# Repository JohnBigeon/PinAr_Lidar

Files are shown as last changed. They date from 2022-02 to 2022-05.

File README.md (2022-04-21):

# PinAr_Lidar

<p float="left">
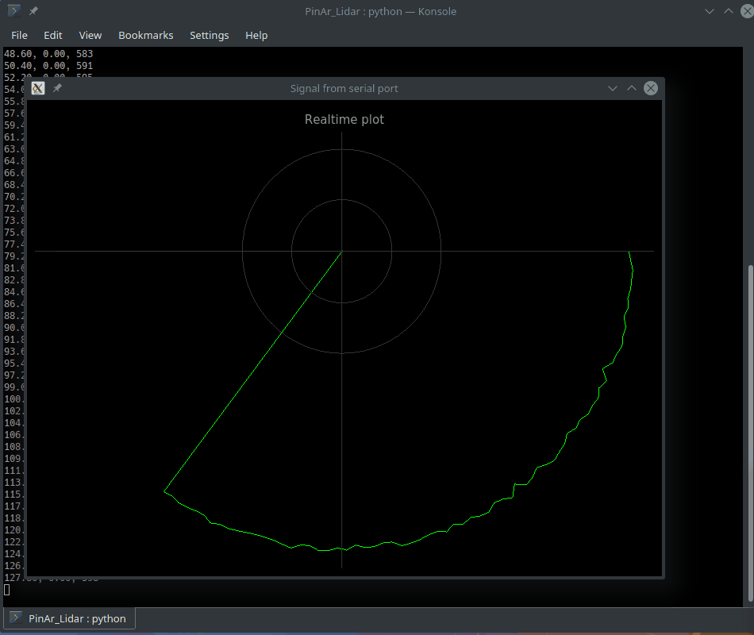
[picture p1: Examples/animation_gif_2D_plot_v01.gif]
  
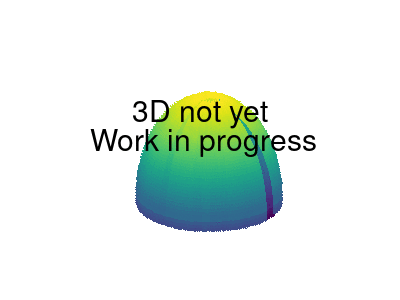
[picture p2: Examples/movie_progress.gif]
   
</p>

<p float="center">
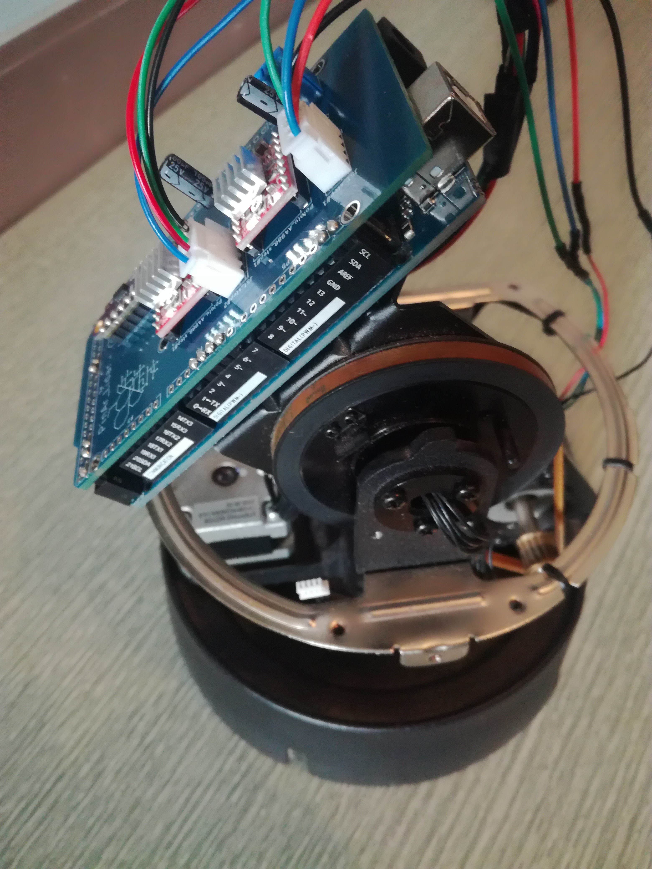
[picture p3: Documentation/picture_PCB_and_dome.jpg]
  
</p>

## Introduction
Here, we will build/assemble a three-dimensional mapping device from a CCTV dome camera setup and a Time-of-Flight (TOF) Distance Sensor to make 2D/3D cartography.

The first question: *Why “hack” a dome camera ?*

First answer, because a dome security camera is designed to monitor a wide range of angles (+/- 360° and +/- 180°). When you open it, you can find two stepper motors with belts, pulleys, and sprockets. All the mechanical parts can be easily hacked to use them as a base for your 2D positionning during cartography of your environment. Second answer, and maybe the best one, this dome was destined for the trash can. In other words, we decide to give a new life to something that will eventually be destroyed.

## Concept
From a pedagogical perspective, let’s start with a static problem. To make a long story short, a TOF setup calculates the distance to an object using time of flight. The time-of-flight principle is based on the time difference between the emission of a signal and its return to the sensor, after being reflected by an object, as presented below. Practically speaking, when a light is emitted from the source, this light will travel through the air until it hits an obstacle which reflects this light. In this case, the time between the emission and the reception is directly related to the distance.

<p float="center">
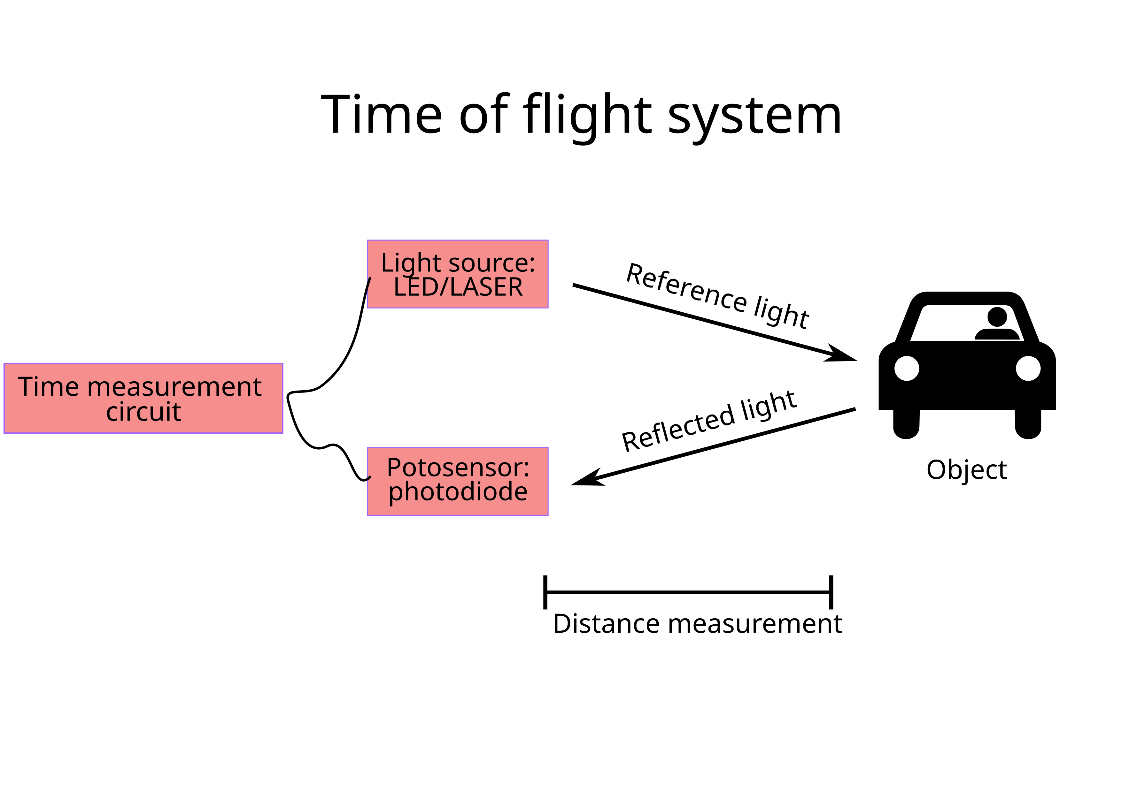
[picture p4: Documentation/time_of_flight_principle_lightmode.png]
  
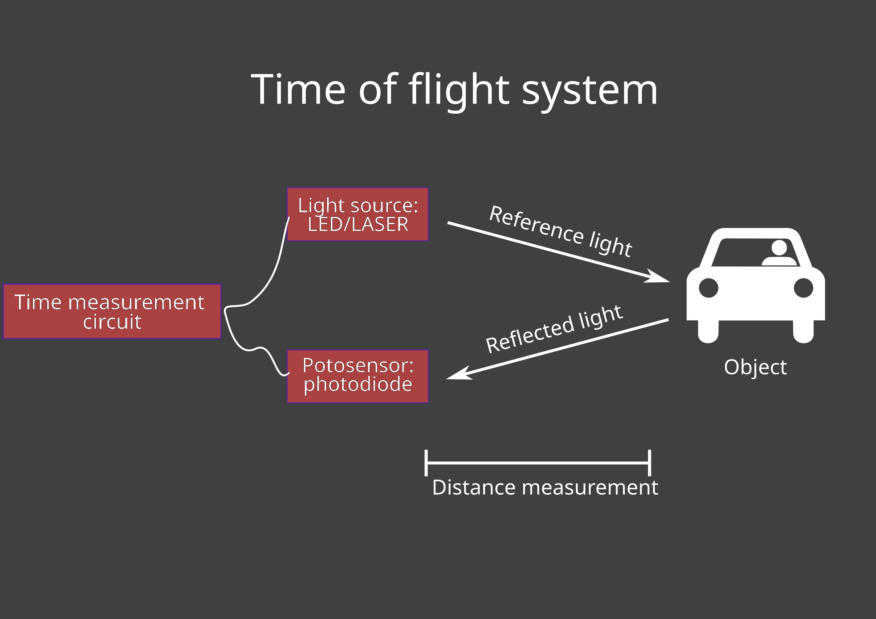
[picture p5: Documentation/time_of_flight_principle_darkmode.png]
  
</p>

Now, aim this source all around you at equally spaced intervals in both the zenithal (theta) and azimuthal (Phi) directions and you can fully determine the distance of objects around you. This is how most of Laser imaging, detection, and ranging (LIDAR) [https://en.wikipedia.org/wiki/Lidar] cartography is done.

From a practical view, the telemetry information is obtained by a Time-of-Flight Distance Sensor (VL5353LXX-V2) and the positioning in the two angular directions sweeping 360 and 180 degrees respectively is achieved by the two stepper motors of the dome system with microstepping driver (Pololu A4988).

## Hardware & Integration
### Dome security camera
<p float="left">
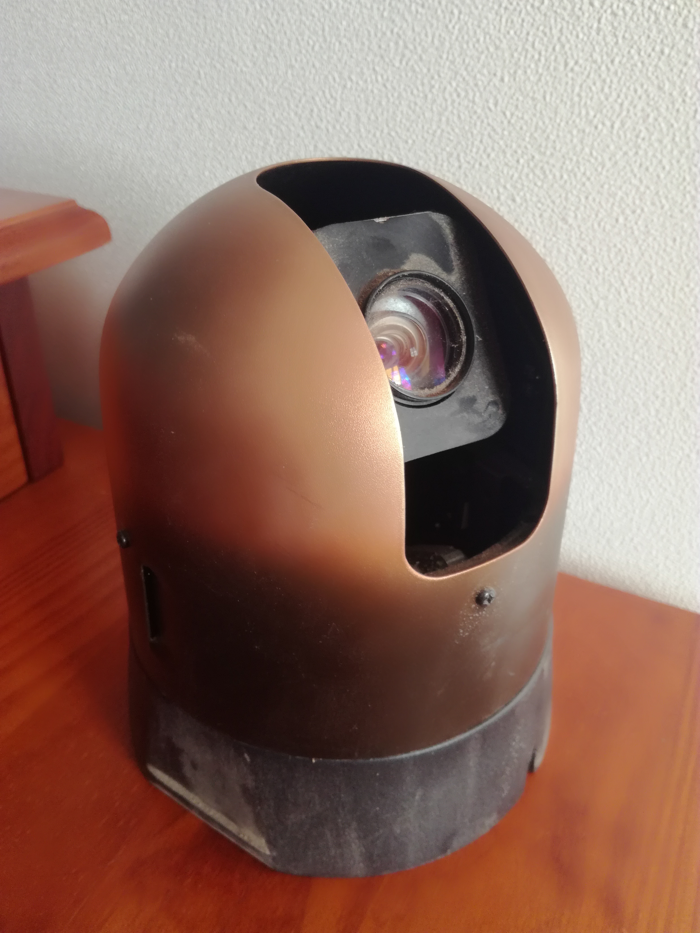
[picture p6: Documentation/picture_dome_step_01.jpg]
  
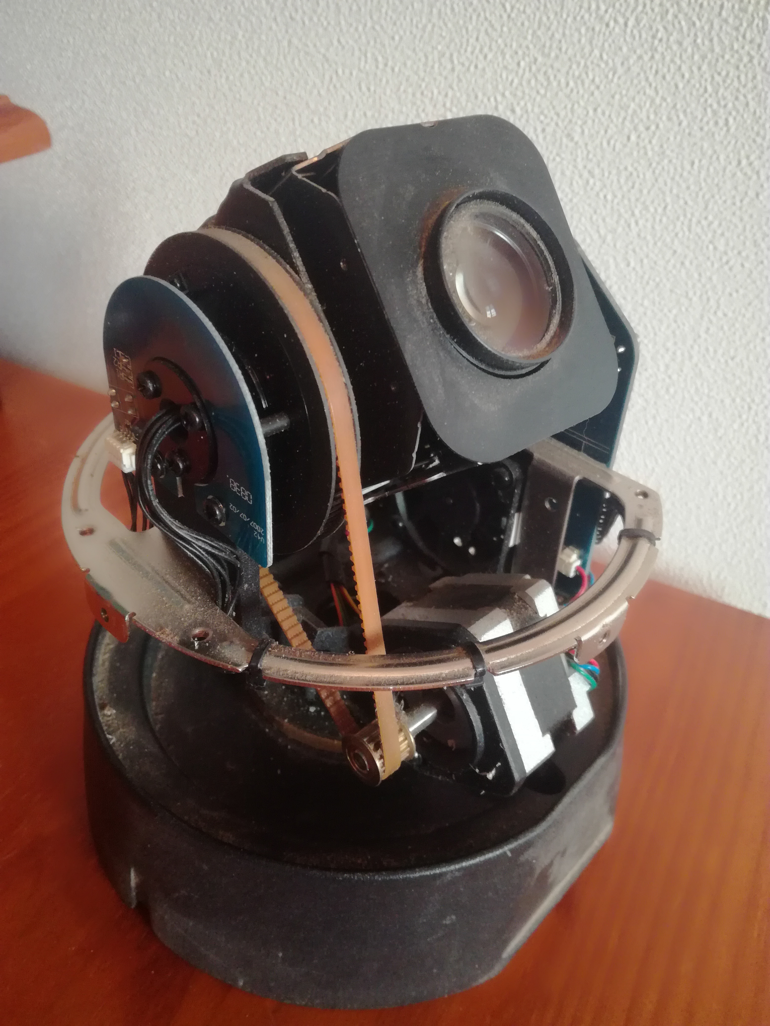
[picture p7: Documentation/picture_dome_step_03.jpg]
   
</p>

### Price
```
         Object           Price (€)
-----------------------   -----
            Arduino MEGA - 18
         Rotation system - 0 
     Power supply 12V 2A - 10
            Pololu A4988 - 3.50
 AZDelivery VL5353LXX-V2 - 9
    Capacitors ( 100 µF) - 1
                  Cables - 1
```
### Motors
<p float="left">
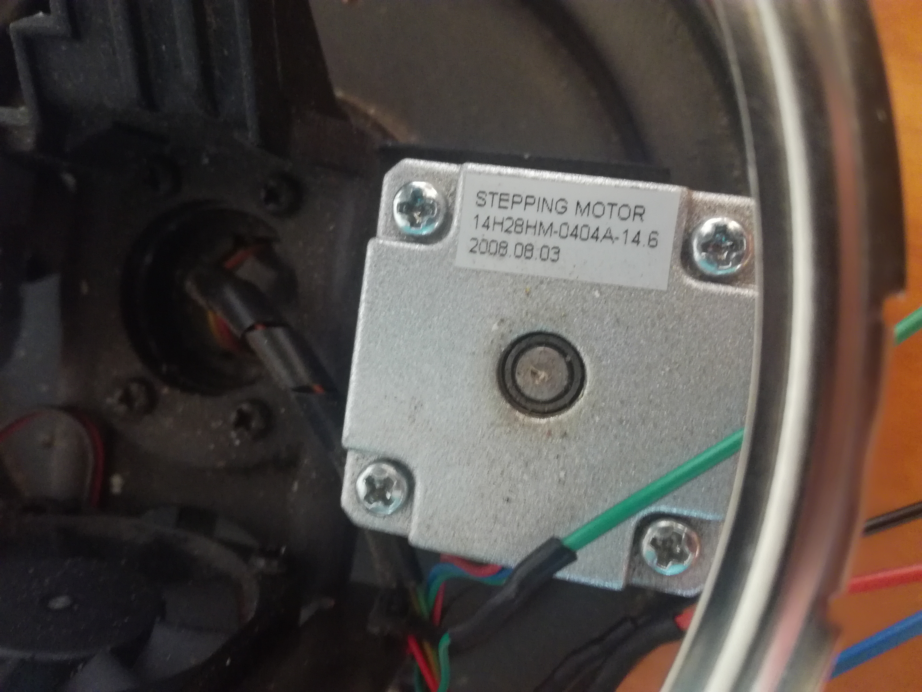
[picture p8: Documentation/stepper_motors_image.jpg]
  
   
</p>

### Power supply
Stepper drivers are power converters, you need to do the calculation in terms of power consumption, not current as explained here [https://forum.arduino.cc/t/what-powersupply-do-i-need-to-power-multiple-stepper-motors/868595/9]. 

Using the power law:
```
P = U x I = 5 x 0.4 = 2 W (per motor/per phase)
```
Here, we are using two stepper motors, the power supply needs to be at least:
````
P_tot = 2 motors * 2 phase * 2W (per motor/per phase) = 8 W
````
Considering the fact that the motors will not always run in parallel, the power consumption is acceptable in our case. In other words, in a 2 axis system, not all motors are working at the same time, same load, meaning that the power value can be lower.
Higher voltage supply allows for faster operation of the steppers, 24V is a commonly chosen supply voltage for a reasonable compromise. If you chose 12V supply, 1.5 A would be appropriate.

**Be careful**, connecting or disconnecting a stepper motor while the driver is powered can **damage** or **destroy** the driver.

### Microstepping
<p float="center">
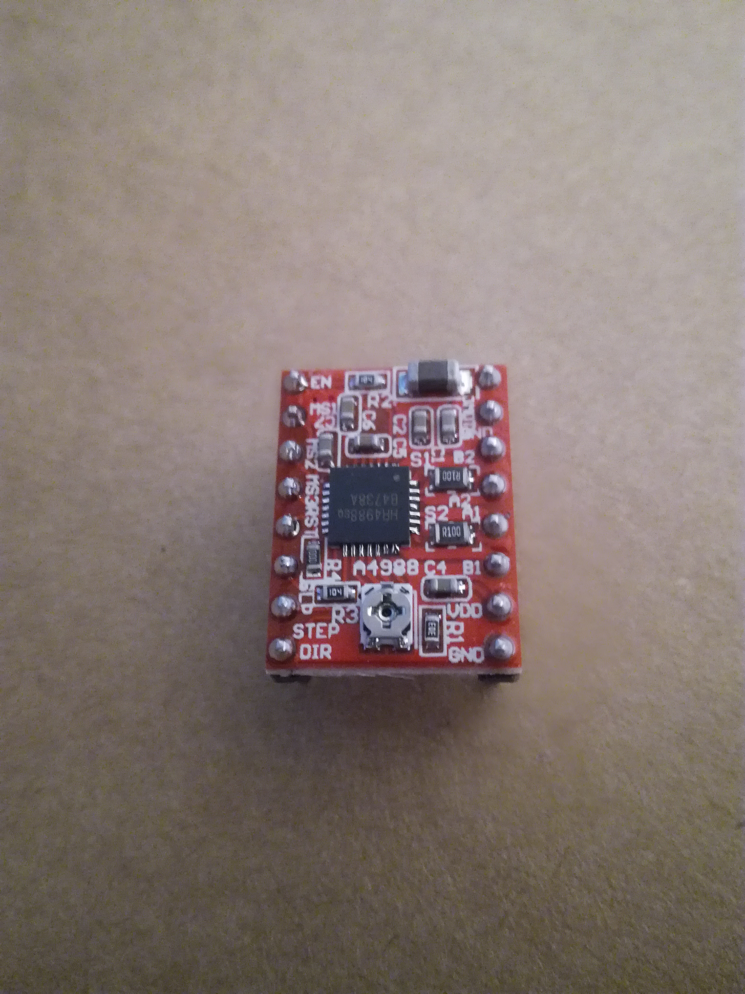
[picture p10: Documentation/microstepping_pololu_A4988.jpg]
  
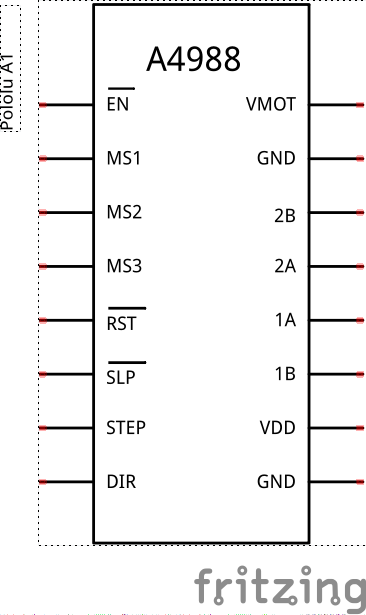
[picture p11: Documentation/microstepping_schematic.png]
  
</p>
<p float="center">
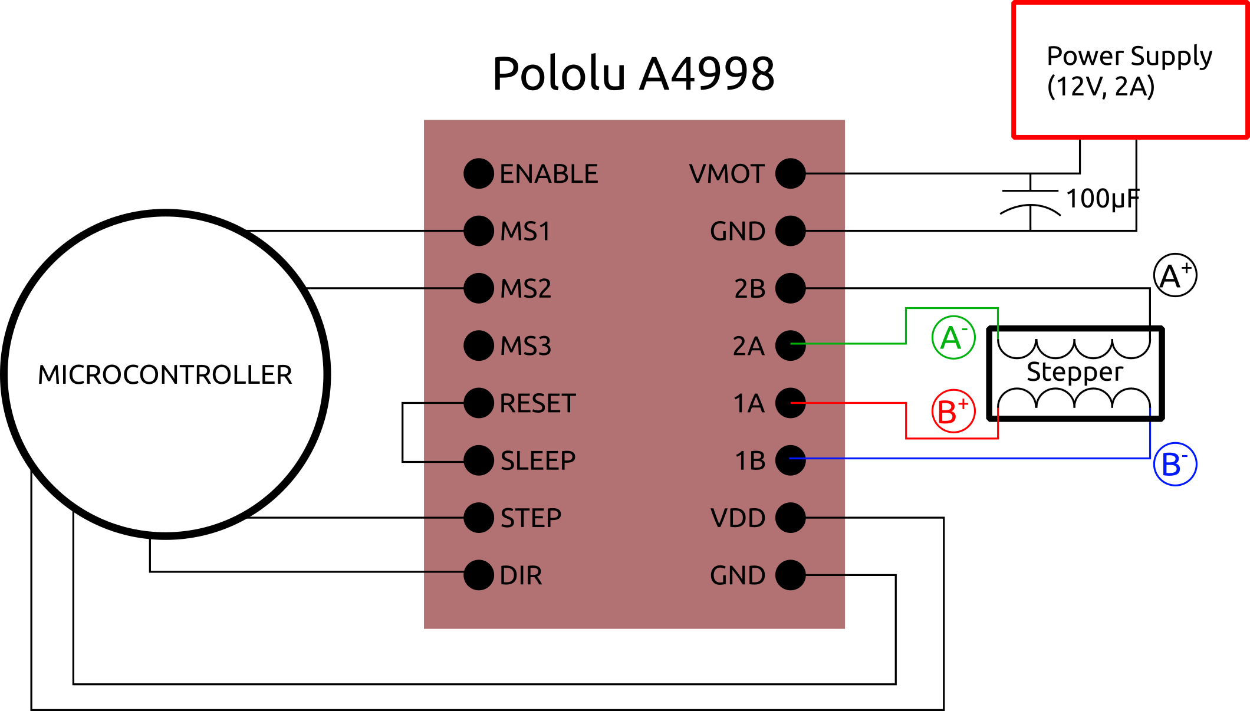
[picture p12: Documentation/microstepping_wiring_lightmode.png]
  
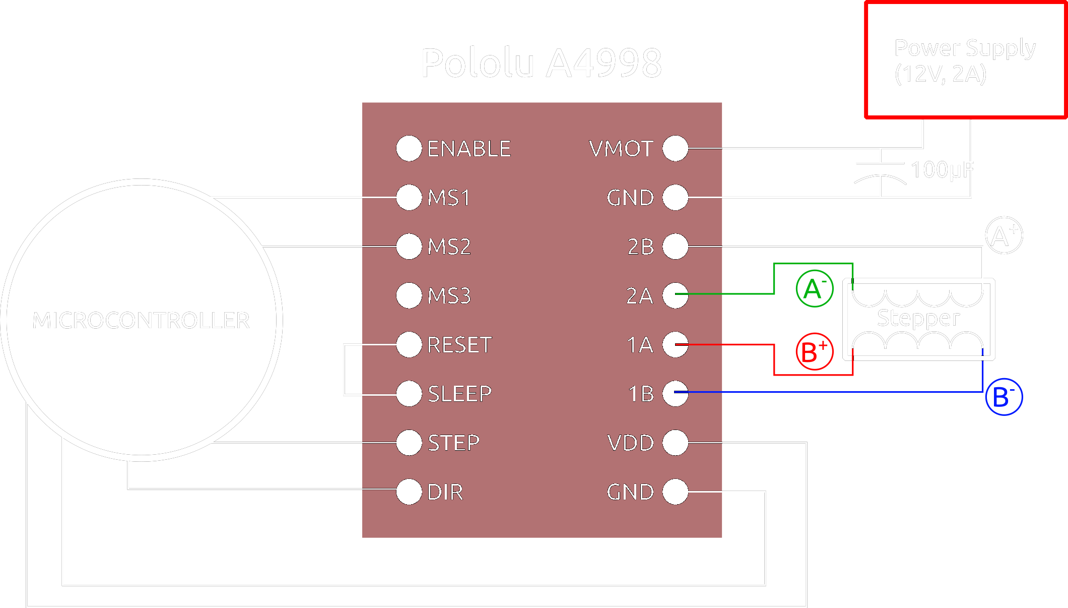
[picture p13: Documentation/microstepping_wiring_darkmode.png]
  
</p>

The first part is to connect and interface stepper drivers (A4988) to the two stepper motors. These stepper motors are able to provide 400 steps per revolution with a resolution of 0.9°. Based on the nice tutorial found here [https://howtomechatronics.com/tutorials/arduino/how-to-control-stepper-motor-with-a4988-driver-and-arduino/], the use of the A4988 stepper driver gives you higher resolution of stepping.
The resolution of the system can be tune by MS1, MS2 and MS3 pins as follow [https://www.robotshop.com/media/files/pdf/datasheet-1182.pdf]:

| MS1 | MS2 | MS3 | Microstepping |
| :---: | :---: | :---: | :---: |
| Low | Low | Low | 1/1 step |
| High | Low | Low | 1/2 step |
| Low | High | Low | 1/4 step |
| Low | Low | High | ??? step |
| High | High | Low | 1/8 step |
| High | High | High | 1/16 step |

As an example, when MS1 and MS2 are connected and not the MS3, the stepping step will be multiply by a factor 8.
 
### Wiring
Concerning the circuit, the 1A and 1B pins will be connected to the first coil of the motor and the 2A and 2B pins to the second. To protect the microstepper driver from voltages spikes, a capacitor (100 µF) is used here. The pin of step and direction of the first stepper driver are connected to the 3 and 4 pins of the Arduino board. For the second stepper driver, they are connected to pins 6 and 5. For both of them, the reset and sleep pins are need to be pulled high (default low are to reset and sleep). Finally, the sensors is directly connected to SCL and SDA pins.
```
A4988 (#1)   Arduino   Power supply
----------   -------   ------------
      VMOT -         - 12V
       GND -         - GND
       VDD - 5V
       GND - GND
       MS1 - DG44
       MS2 - DG46
      STEP - PWM6
       DIR - PWM5
```
```
A4988 (#2)   Arduino   Power supply
----------   -------   ------------
      VMOT -         - 12V
       GND -         - GND
       VDD - 5V
       GND - GND
       MS1 - DG24
       MS2 - DG26
      STEP - PWM3
       DIR - PWM4
```
```
Arduino   VL53LXX-V2 board
-------   -------------
    5V  - VIN
    GND - GND
    SDA - SDA
    SCL - SCL
```

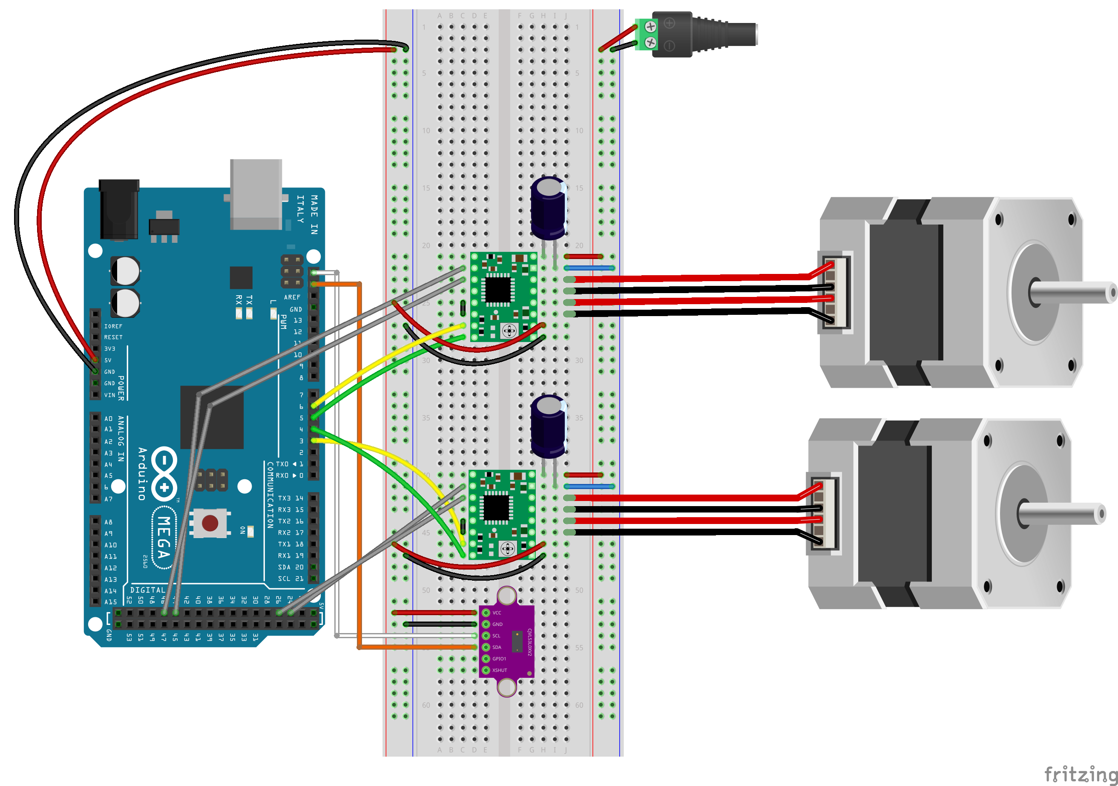
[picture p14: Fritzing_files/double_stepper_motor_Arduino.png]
fritzing


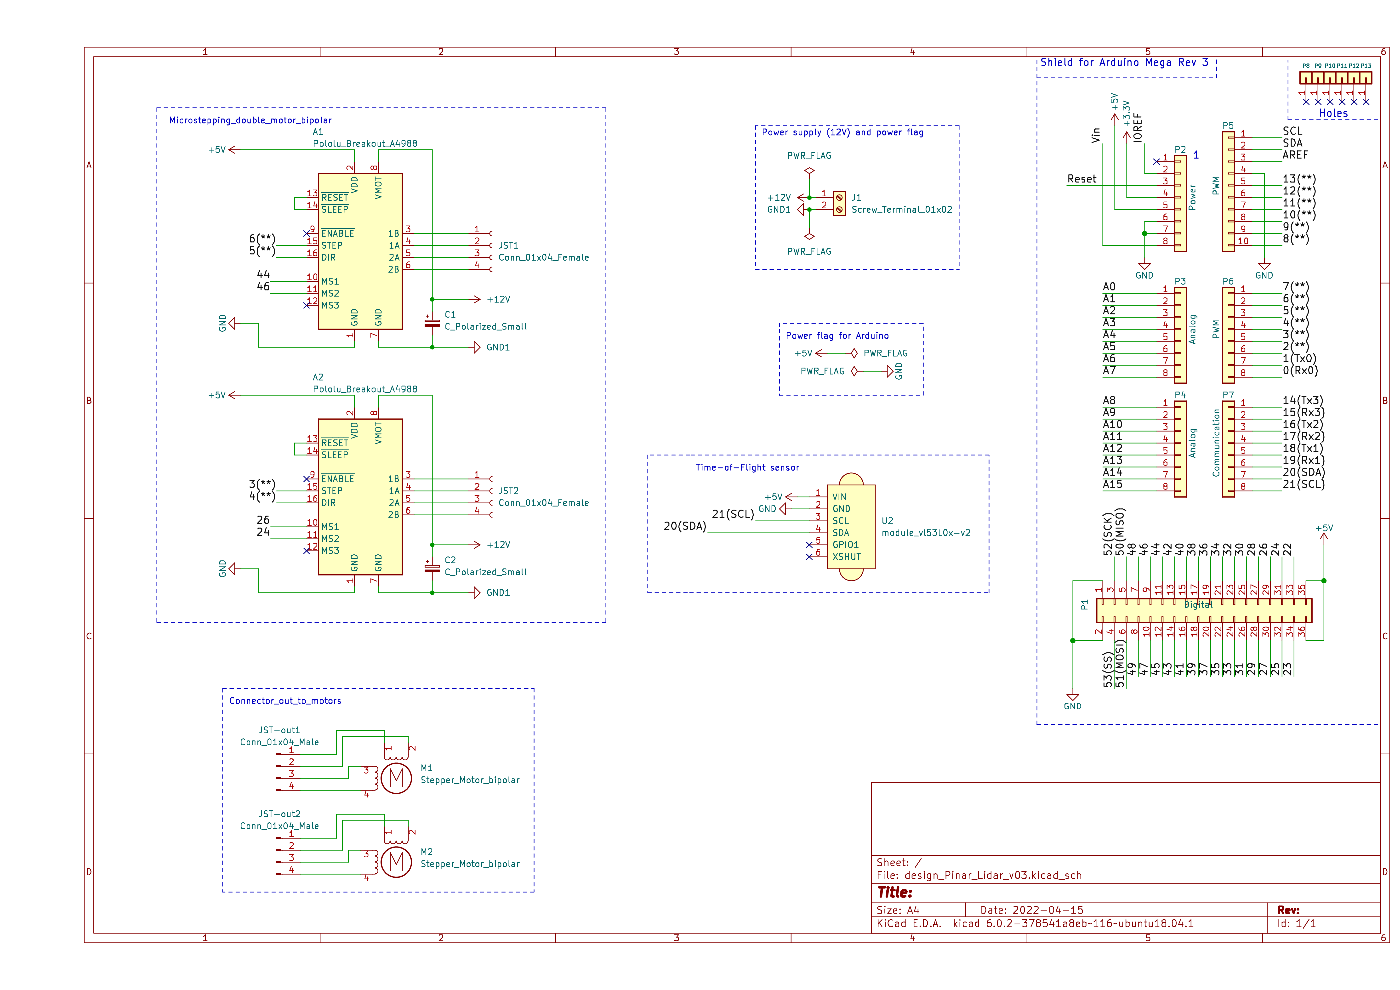
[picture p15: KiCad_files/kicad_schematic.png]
KiCad


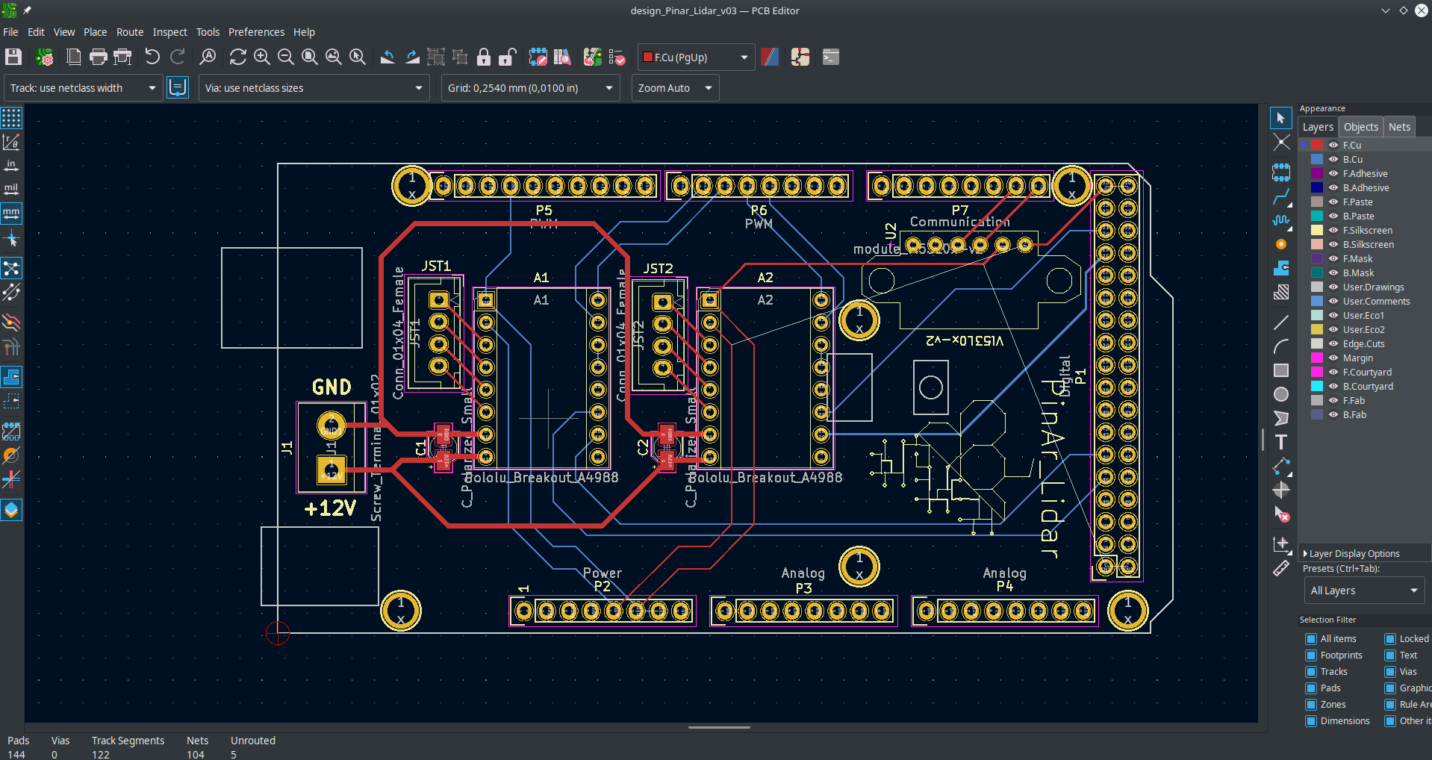
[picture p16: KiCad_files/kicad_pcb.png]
PCB


##### Coil resistance
To confirm the wiring and specially 2B/2A/1A/AB, we can check the coil resistance simply by measuring the resistance across any two wires. As visible here, the Blue and Green wires are associated and if you try any other pairs, you should read the famous 'OL' Infinite resistance (open circuit).
<p float="center">
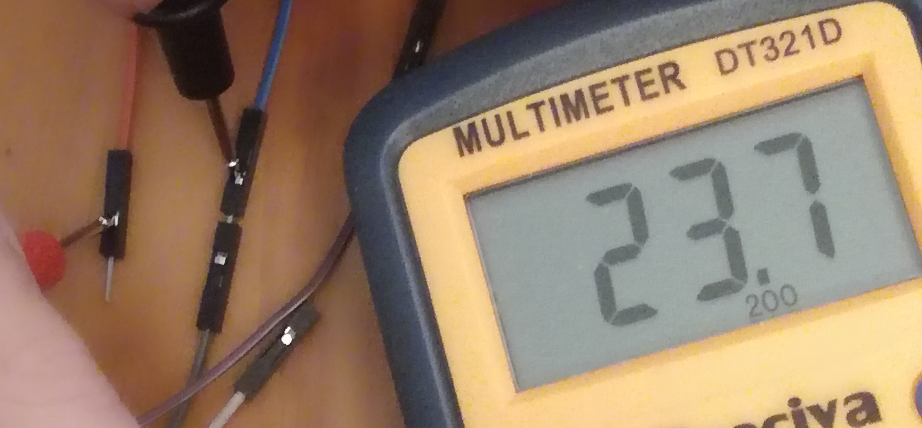
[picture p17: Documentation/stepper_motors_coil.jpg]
  
</p>
 
#### Set max current
To prevent overheating of your motors (and then, their durability), it is necessary to ensure that there are an adequate current limitation on your A4988 boards. All explanations can be found in the video [https://howtomechatronics.com/tutorials/arduino/how-to-control-stepper-motor-with-a4988-driver-and-arduino/].
This stepper driver allows tuning of the maximum current as explained here [https://www.rototron.info/raspberry-pi-stepper-motor-tutorial/] or here [https://lastminuteengineers.com/a4988-stepper-motor-driver-arduino-tutorial/] in order to protect your board of destructive voltage spikes.
My protocol is:
- Set the current limit by measuring the voltage (Vref) on the “ref” pin and the microstep pins disconnected. 
- Take a look at the datasheet for your stepper motor and specially the rated current.
- Measure the voltage (Vref) on the metal trimmer pot itself while you adjust it. 
- Adjust the Vref voltage using the formula:
```
Current Limit = Vref x 2.5
```
In our case, the motor is rated for 400mA, and the reference voltage is fixed to 0.16 V.
```
V_ref = 0.4 / 2.5 =  0.16 V
```
Generally, if the motors are noisy, too hot while stepping or missing steps that means the current limiting is set incorrectly. 

### Reduction gear
This dome use a reduction gear and the big gear has six times the diameter of the small one (giving a 6:1 ratio). In our case, a full rotation (360°) is equal to
````
360 steps = 360 / resolution * gear = 360 / 0.9 * 6 = 2400
````

### First integration
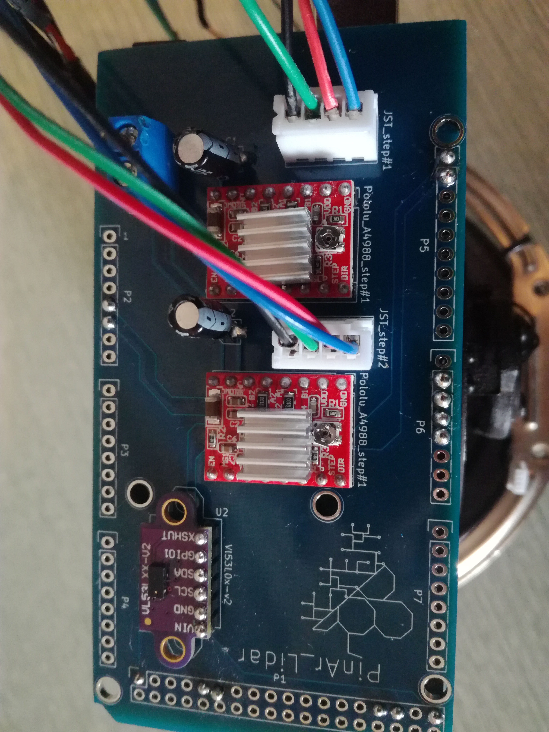
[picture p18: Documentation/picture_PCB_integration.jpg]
Integration


### Simple test to control Stepper Motor and spin Direction
This code will also help you to fix the delay during the stepping process.
Arduino code (see 'Rotation_stepper_simple' folder):
```
//==============================================================================
//title              :one_stepper_rotation_v01.ino
//description        :Control one stepper motor with A4988
//                   :Inspired by https://how2electronics.com/control-stepper-motor-with-a4988-driver-arduino/
//author             :John Bigeon  (https://github.com/JohnBigeon/PinAr_Lidar)
//date               :20220206
//version            :for arduino MEGA (tested on 1.8.19 @ubuntu)    
//usage              :
//script_version     :0.9-release
//Output             :Control stepper motor
//notes              :MS1, MS2 and MS3 are LOW
//==============================================================================

const int dirPin = 6;
const int stepPin = 5;
const int stepsPerRevolution = 2400;
 
void setup()
{
  // Declare pins as Outputs
  pinMode(stepPin, OUTPUT);
  pinMode(dirPin, OUTPUT);
}
void loop()
{
  // Set motor direction clockwise
  digitalWrite(dirPin, HIGH);
 
  // Spin motor slowly
  for(int x = 0; x < stepsPerRevolution; x++)
  {
    digitalWrite(stepPin, HIGH);
    delayMicroseconds(2000);
    digitalWrite(stepPin, LOW);
    delayMicroseconds(2000);
  }
  delay(1000); // Wait a second
  
  // Set motor direction counterclockwise
  digitalWrite(dirPin, LOW);
 
  // Spin motor quickly
  for(int x = 0; x < stepsPerRevolution; x++)
  {
    digitalWrite(stepPin, HIGH);
    delayMicroseconds(1000);
    digitalWrite(stepPin, LOW);
    delayMicroseconds(1000);
  }
  delay(1000); // Wait a second
}
```
Make sure after few minutes that the motor temperature is fine and that no steps have been missed during the rotation (i.e.: the full rotation needs to be equal to 360°).

## Software
The code is separated in two different entities: an arduino code which gives you the measured distances at every step of motors and the python code to display a pretty interface in real time.
The arduino has been tested on arduino-1.8.19 for ubuntu and *arduino-XXX* for Windows 10.

### Arduino code
#### Third-party dependencies: Packages and librairies
Use the Library Manager to install the library *VL53L0X by Pololu (version 1.3.0)* [https://github.com/pololu/vl53l0x-arduino] on the  Arduino Software (IDE).

#### First test
Once the arduino code (folder *Arduino_code*) is uploaded to the board, open your Serial Monitor and you should see something like that:
```
Welcome aboard to Air PinAr_Lidar, 3D positioning
Ignition, what is my purpose ?
Test (T) ? Fast 2D (F) ? Precise 3D (P) ? nb: Emergency case (X) 
```
To confirm that you have successfully integrated your board to the hardware component, use the test configuration by hitting the T and Enter characters of your keyboard in the console (No line ending). If your stepper motors perform the 180° movement in theta direction and the 90° in phi direction, WELL DONE ! In other cases, please see the section “Well-known bugs”.

Here, the position of each stepper motors is converted in spherical coordinate system (theta and phi). Every lines sent from the Arduino to serial monitor consists of phi and theta positions and distance.
So, during this test, you may have seen in the monitor, information about angle positions and distance as:
Theta position (°) Phi position (°) Distance (cm)
```
16.0		00.0 		225.0
16.0		00.9 		201.0
...
```
##### Explore different configurations
We designed four modes of configuration for our mapping system:
- The test configuration (T) where motors make a movement of 180 degrees in theta and 90 degrees in phi direction. It’s useful to check if your board and the microstepping is correctly connected.
- A fast cartography (F), where you measure distance from the dome according a 180-degree angle in the theta direction. 
- A full and precise (P for precise) cartography of space, which means 360 degrees over theta and 90 degrees over phi.
- The shutdown mode (X) where two steppers will return to the starting position.
These modes can be directly called by X, F, P or T characters in the baud of arduino.

### Python code
#### Third-party dependencies: Packages and librairies
To provide a visual interface to our cartography, we decide to use a *python interface*. The reason to do that is mainly because *python* is highly extensible [https://en.wikipedia.org/wiki/Zen_of_Python] and commonly used in Science or Engineering.
The python codes will command the configuration needed by sending the character X, T, F or P and read every values in the baud port. One important point to be stressed is the difficulty for matplotlib to display a figure at high speed rate, typically at more than 10 figures per second. In order to display the distance as fast as we can, we decided to use pyqtgraph packages [http://www.pyqtgraph.org/]. 
To run these scripts, the easiest way is to create a virtual conda environment [https://docs.conda.io/projects/conda/en/latest/user-guide/getting-started.html] with all packages required.
To install theses packages, you have two option, load our environment here and use the command:
```
conda env create -f list_lidar_env.yml
```
or do it manually by:
```
conda create --name lidar_env python=3.7 numpy spyder matplotlib pyqtgraph pyserial tqdm
```
Now, you can simply activate your virtual environment by the command:
```
conda activate lidar_env
```
You also need the package “drawnow”, not available on the conda package manager. To install it, use: 
```
pip install drawnow
```

## Usage
XXX

### 2D scanning
In your python environment, use the command:
```
python plot_2d_radar_vXXX.py
```
Here, your mapping system is gathering distance at every angles defined by the motor in theta direction and display it in real time. To **shutdown** your measure, hit **Ctrl+C** in your console. That will close the baud and let motors going to initial positions.

### 3D scanning
In your python environment, use the command:
```
python plot_3d_animation_vXX.py
```
Here, your mapping system is gathering distance at every angles defined by the motor in theta direction and phi direction, but save theses informations in a csv file. Once you have finished the cartography or decided to cancel it (by Ctrl + C), the cartography is displayed on a matplotlib window and on a gif in your directory file.

### Well-known bugs
#### Stepper motor is not actually moving correctly.
- Check the connection of your motor.
- Increase the delay between two pulses send to motor for stepping. In Arduino code, modify the line 34:
      int delay_switch = 1000;
- Use *delayMicroseconds()* and not *delay()* between the two pulses

#### Noise removal and readings that are far away from mean value are removed
TODO

#### Monitor return return the value NACK
- Check the LIDAR connection.

#### Problem to upload the arduino code to your board
- Carefully use the good board type & port in the menu of the Arduino IDE.

#### Uploading code to arduino gives me errors
- On fresh ubuntu installation, you may experience minor problems, that can fixed following this [https://askubuntu.com/questions/1056314/uploading-code-to-arduino-gives-me-the-error-avrdude-ser-open-cant-open-d].
    
### Future improvements
* Use enable pin of A4988 to reduce power consumption.
* Use battery as power supply ?
* Use a Bluetooth module to replace the wired connection for transmitting serial data.

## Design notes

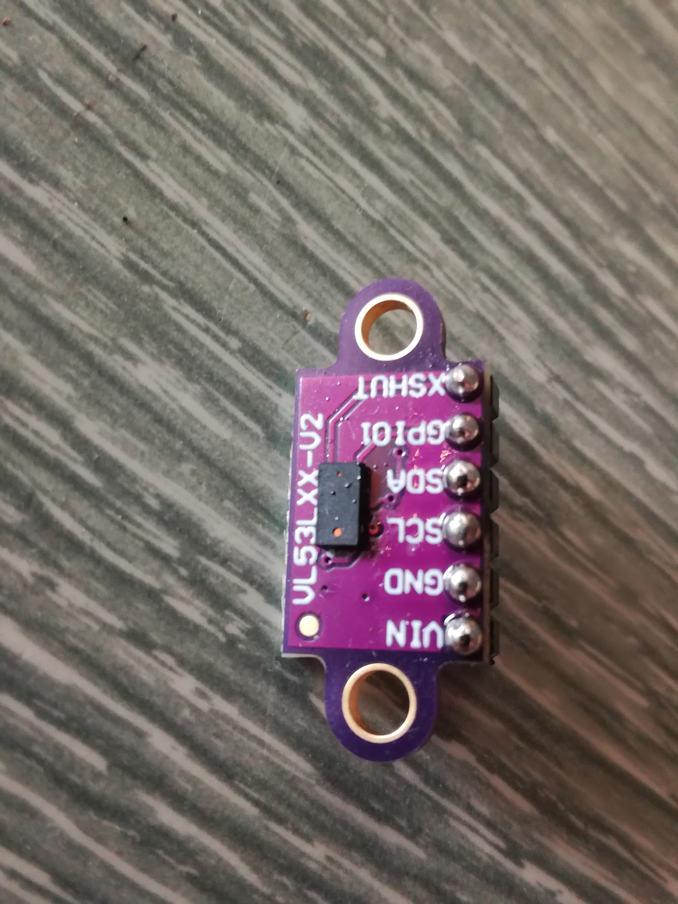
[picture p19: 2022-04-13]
Documentation/picture_VL53LXX-v2.jpg

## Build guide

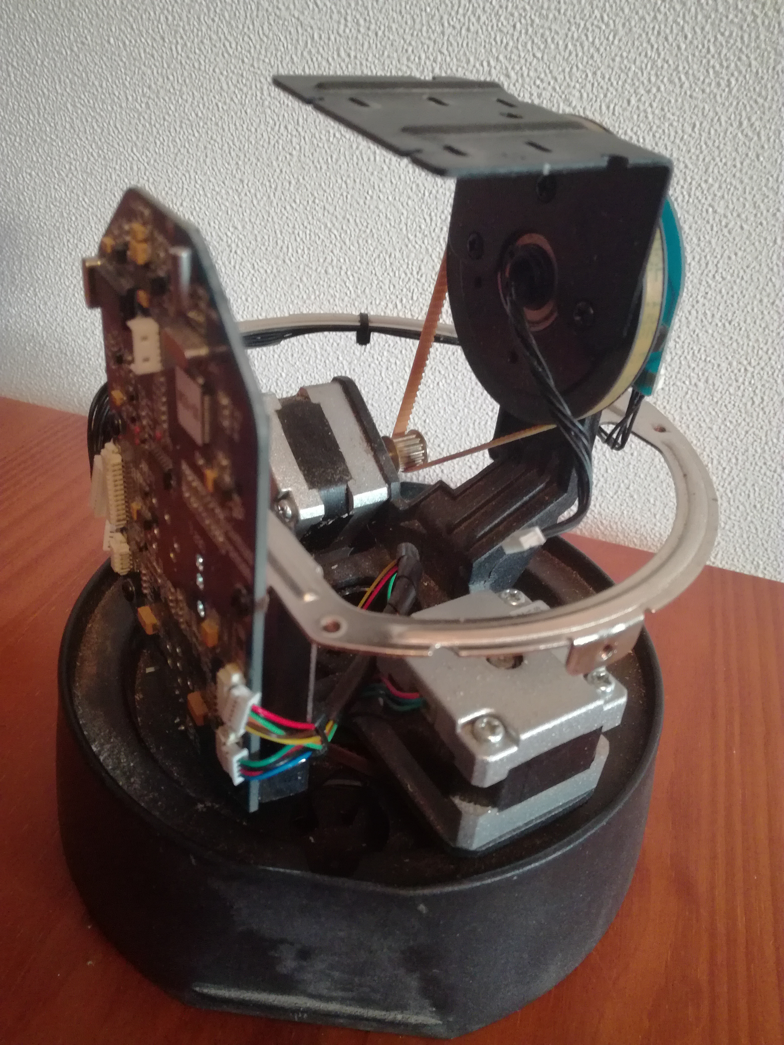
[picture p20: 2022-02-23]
Documentation/picture_dome_step_04.jpg

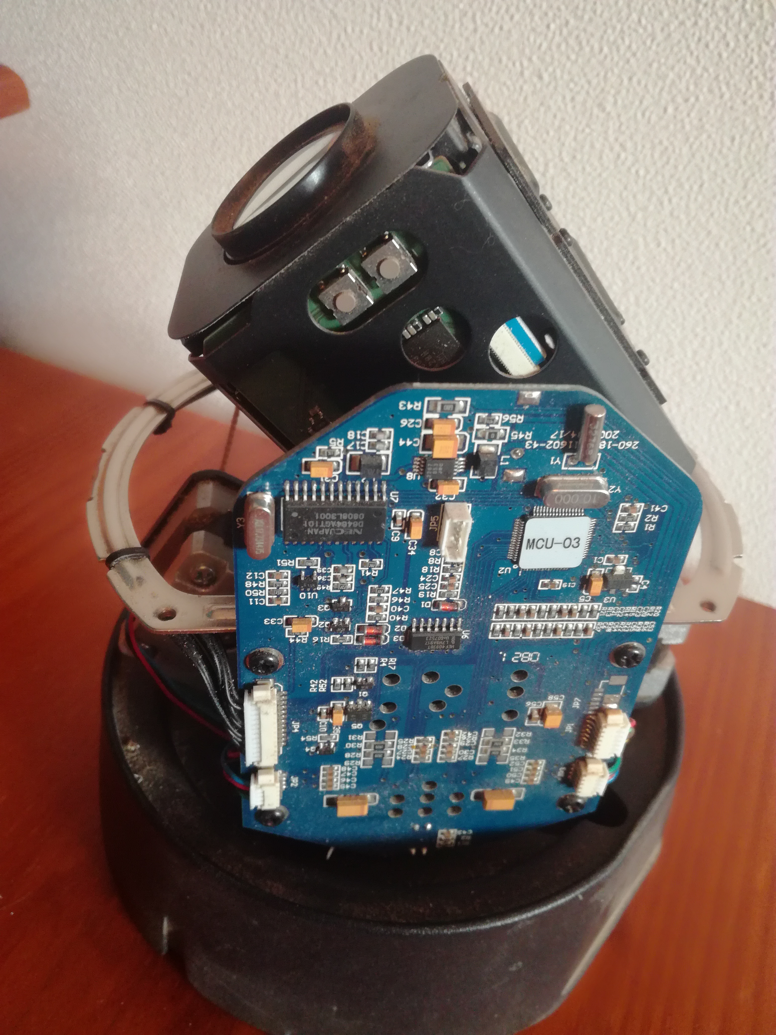
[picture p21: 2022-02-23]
Documentation/picture_dome_step_02.jpg

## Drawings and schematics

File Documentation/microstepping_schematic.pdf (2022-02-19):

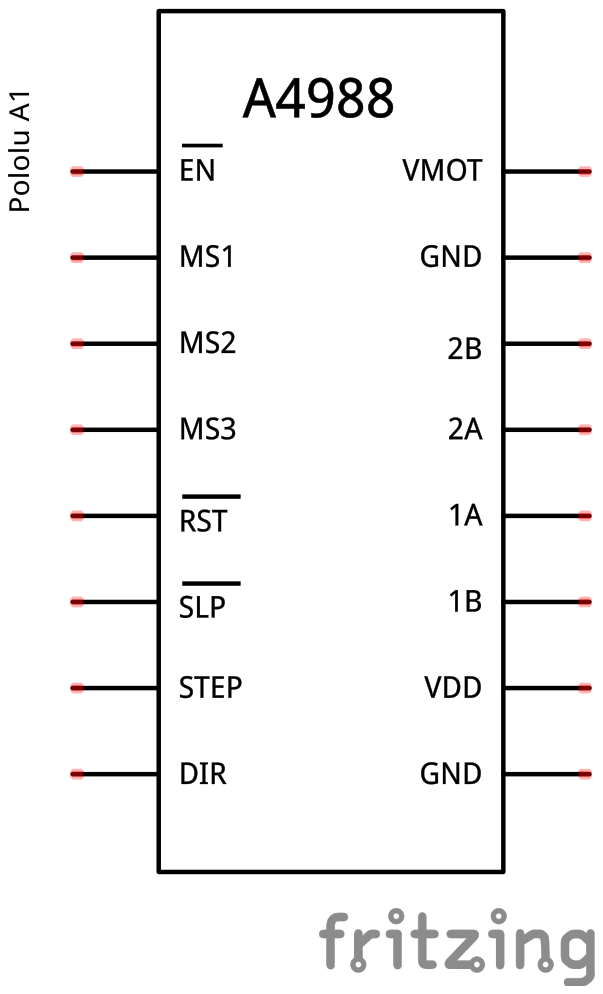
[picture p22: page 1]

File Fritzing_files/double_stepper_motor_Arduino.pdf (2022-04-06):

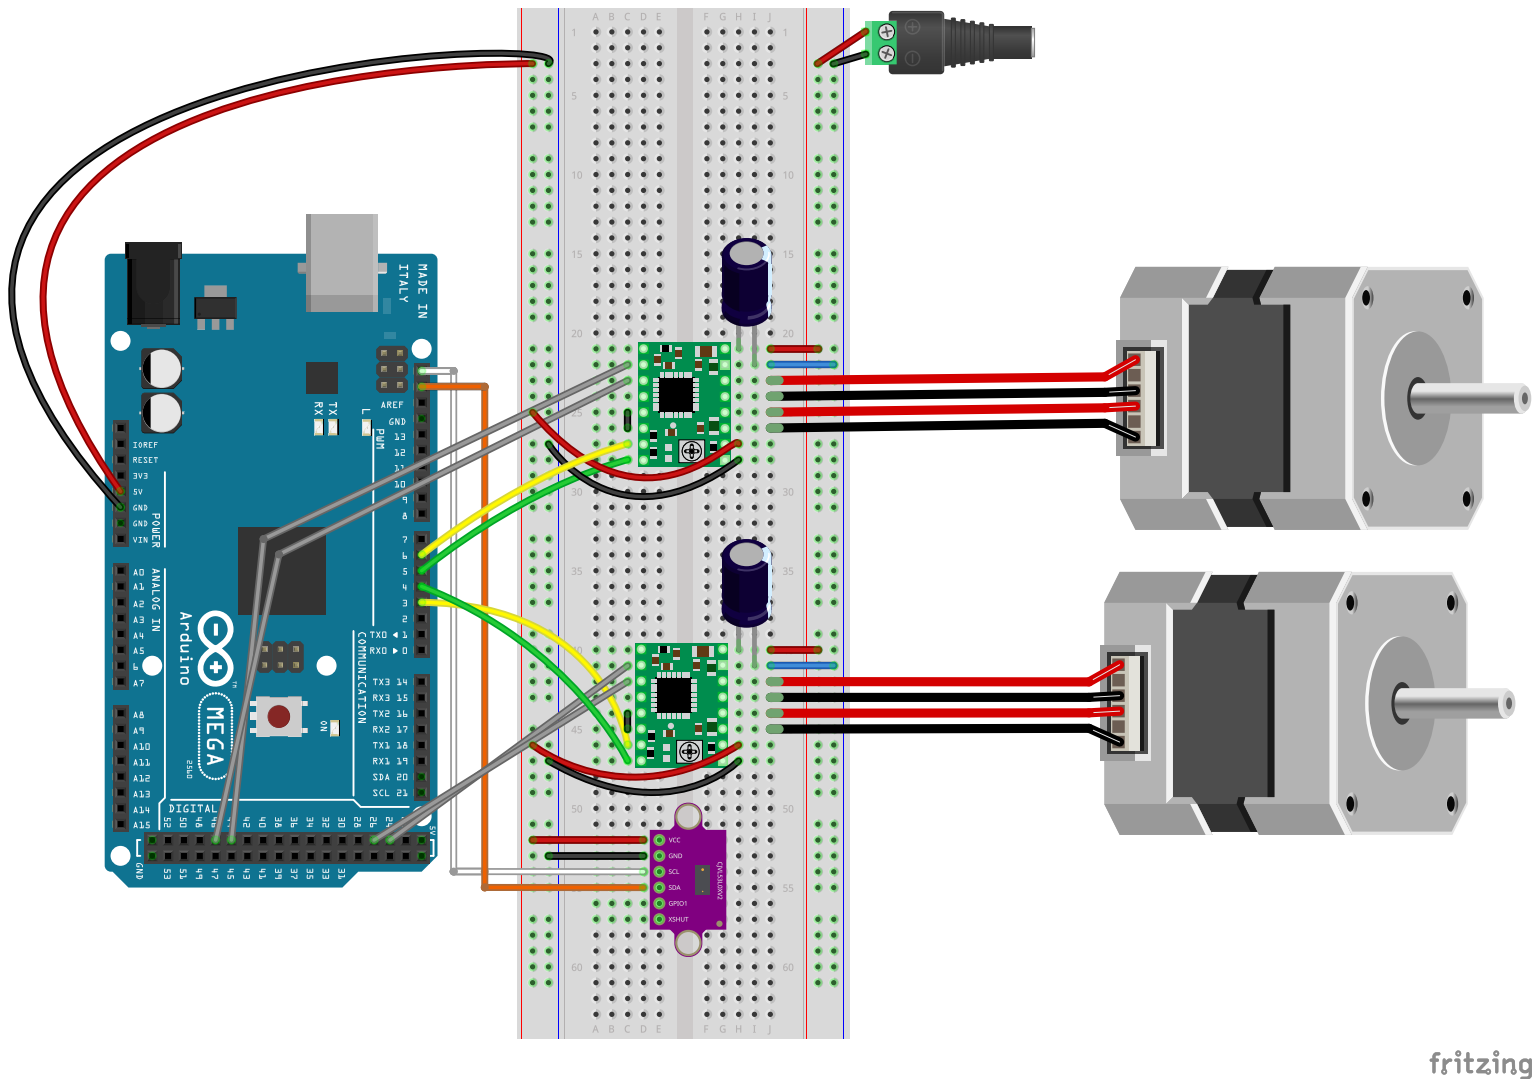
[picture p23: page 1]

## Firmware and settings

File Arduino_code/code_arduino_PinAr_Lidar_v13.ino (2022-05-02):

//==============================================================================
//title              :lidar_v13.ino
//description        :Control two stepper motor with A4988 for mapping
//                   :Read distance from VL53LXX-V2
//author             :John Bigeon	(https://github.com/JohnBigeon/PinAr_Lidar)
//date               :20220421
//version            :for arduino MEGA (tested on 1.8.19 @ubuntu)    
//usage              :library required: VL53L0X by Pololu (version 1.3.0)
//script_version     :0.9-release
//Output             :Control stepper motor
//notes              :Problem with conversion of floats to string with old version (native with linux !!!)
//==============================================================================
// -*- coding: utf-8 -*-/
#include <Wire.h>
#include <VL53L0X.h>

//==============================================================================
// Globals
//LIDARLite lidarLite;
VL53L0X sensor;

//Variable declaration
int microstepping   = 1;       //XXX The stepper driver configuration (microstepping=8, 4, 2 or 1)
int cal_cnt = 0;
int gear_reduc = 6;
int fullcycle_theta = 200*microstepping*gear_reduc;    // number of step for full cycle for 360deg/0.9deg=200steps
int fullcycle_phi   = 200*microstepping*gear_reduc;    // number of step for full cycle for 360deg/0.9deg=200steps
float resol         = 0.9/(microstepping*gear_reduc);    // resolution of stepper
int pos1_init       = 0;        // position initial of first  motor
int pos2_init       = 0;        // position initial of second motor
int pos1            = 0;        // position of first  motor
int pos2            = 0;        // position of second motor
float pos1r         = 0;        // position of first  motor in degrees
float pos2r         = 0;        // position of second  motor in degrees
int mydelay         = 2000;       // (microseconds) time we are waiting at precise position
int delay_switch    = 5;        // (ms) time between two pulses send to motor for stepping
int incomingByte    = 0;    // for incoming serial data
int delaybackward   = 1000;
String action;   //Declare a String variable to hold your name

//==============================================================================
// For stepper 1
//#define pin1Enable 13 // Activation du driver/pilote
#define pin1Step    3   // Step
#define pin1Dir     4   // Direction 
#define pin1MS1     44
#define pin1MS2     46

// For stepper 2
#define pin2Step    6   // Step
#define pin2Dir     5   // Direction 
#define pin2MS1     26
#define pin2MS2     24

// Pin 13 has an LED connected on most Arduino boards
int led = 13;

//==============================================================================

void setup(){
    Serial.begin(9600);  // turn on Serial Port
//    lidarLite.begin(0, true); // Set configuration to default and I2C to 400 kHz
//    lidarLite.configure(0); // Change this number to try out alternate configurations
    Wire.begin();

    sensor.setTimeout(500);
    if (!sensor.init())
    {
        Serial.println("Failed to detect and initialize sensor!");
        while (1) {}
    }
    Serial.println("Welcome aboard to Air PinAr_Lidar, 3D positioning");
    
    // initialize the digital pin as an output
    pinMode(led, OUTPUT);  
  
    // Initialisation of stepper1
    pinMode(pin1Dir , OUTPUT);
    pinMode(pin1Step, OUTPUT);
    pinMode(pin1MS1, OUTPUT);
    pinMode(pin1MS2, OUTPUT);
  
    // Initialisation of stepper2
    pinMode(pin2Dir, OUTPUT);
    pinMode(pin2Step, OUTPUT);
    pinMode(pin2MS1, OUTPUT);
    pinMode(pin2MS2, OUTPUT);

    Serial.setTimeout(10); // dont wait too long for emergency case
}

//==============================================================================
//Here comes the sun
//==============================================================================

void loop(){
    int dist;
    int i = 0;
    int j = 0;
    
    // To display and communicate
    String stringpos1txt = "motor1 pos: "; 
    String stringpos2txt = "motor2 pos: "; 
    String sensorvaltxt  = "sensor val: ";
    String separator     = ", ";
    
    // Stepper initialisation
    digitalWrite(pin1Step, LOW);
    digitalWrite(pin2Step, LOW);

    // Init. MS1 & MS2
    microstepping_config(microstepping);
    
    // Blink to say Hello
    digitalWrite(led, HIGH);   // turn the LED on (HIGH is the voltage level)
    delay(1000);               // wait for a second
    digitalWrite(led, LOW);    // turn the LED off by making the voltage LOW
    delay(1000);               // wait for a second

 

    // Select a command to do
    Serial.println("Ignition, what is my purpose ?");
    Serial.println("Test (T) ? Fast 2D (F) ? Precise 3D (P) ? nb: Emergency case (X)");

    while(Serial.available()==0){       // Wait for User to input data
    // send data only when you receive data:
    }

    action=Serial.readString();         //Read user input into action
    Serial.println(action);
 
    
    if (action == "T" || action == "F" || action == "P"){


        if (action == "T"){
          
          digitalWrite(pin1Dir, HIGH); // Direction forward
          
          for (i=0; i<fullcycle_theta + 1; i++){
              
              pos1 = pos1_init + i;
              pos2 = 0;
       
              // Read the value from the sensor
              dist = sensor.readRangeSingleMillimeters();
             
              // Display real degree, and not step value
              pos1r = pos1 * resol;   pos2r = pos2 * resol;
              String stringpos     = pos1r + separator + pos2r + separator + dist;
              Serial.println(stringpos);
              
              digitalWrite(pin1Step, HIGH);
              delayMicroseconds(mydelay);
              digitalWrite(pin1Step, LOW);
              delayMicroseconds(mydelay);
          }
          delay(1000); // Wait a second
          
          digitalWrite(pin2Dir, HIGH); 
                   
          for(j=0; j<fullcycle_phi/4 + 1; j++){
               
              pos2 = pos2_init + j;
                      
              // Read the value from the sensor
              dist = sensor.readRangeSingleMillimeters();     
                      
              // Display real degree, and not step value
              pos1r = pos1 * resol;   pos2r = pos2 * resol;
              String stringpos     = pos1r + separator + pos2r + separator + dist;
              Serial.println(stringpos);
                    
              digitalWrite(pin2Step, HIGH);
              delayMicroseconds(mydelay);
              digitalWrite(pin2Step, LOW);
              delayMicroseconds(mydelay);
          }
          digitalWrite(led, LOW); Serial.println(""); Serial.println("Job done !");
          homing(i, j);        
        }
        
        if (action == "F") {
           delay(2500);
           String config_com  = "Config microstepping used: ";
           String config_used = config_com + microstepping + " " ;
           Serial.println(config_used);

            delay(5000);  // Wait for User
            while(true) { // never stop the music

                //Serial.println("GogogadjetoFoton !");
                digitalWrite(led, HIGH);   // turn the LED on
                digitalWrite(pin1Dir, HIGH); // Direction forward

                // Fullcycle step for first motor
                for (i=0; i<fullcycle_theta/2 + 1; i++){
          
                    pos1 = pos1_init + i;
                    pos2 = 0;
          
                    // Read the value from the sensor
                    dist = sensor.readRangeSingleMillimeters();

                    // Display real degree, and not step value
                    pos1r = pos1 * resol;   pos2r = pos2 * resol;
                    String stringpos     = pos1r + separator + pos2r + separator + dist;
                    Serial.println(stringpos);

                    
                    digitalWrite(pin1Step, HIGH);
                    delayMicroseconds(mydelay);
                    digitalWrite(pin1Step, LOW);
                    delayMicroseconds(mydelay);
                }

                digitalWrite(pin1Dir, LOW); // Direction backward
                
                // Fullcycle step for first motor
                for (i=0; i<fullcycle_theta/2+1; i++){
          
                    pos1 = fullcycle_theta/2 - (pos1_init + i);
                    pos2 = 0;
          
                    // Read the value from the sensor
                    dist = sensor.readRangeSingleMillimeters();
                    
                    // Display real degree, and not step value
                    pos1r = pos1 * resol;   pos2r = pos2 * resol;
                    String stringpos     = pos1r + separator + pos2r + separator + dist;
                    Serial.println(stringpos);
                    
                    
                    digitalWrite(pin1Step, HIGH);
                    delayMicroseconds(mydelay);
                    digitalWrite(pin1Step, LOW);
                    delayMicroseconds(mydelay);
                }   // Fullcycle step for first motor
                
                // Emergency break
                action=Serial.readString();         //Read user input into action
                if (action == "X"){
                    //homing(i, 0);
                    break;
                }
        }
        digitalWrite(led, LOW); Serial.println("Job done !");
    }
        
///////////////////////////////////////////////////////////////////////////////////////////
        if (action == "P") {
            delay(1000);  //wait user

            Serial.println("GogogadjetoFoton !");
            digitalWrite(led, HIGH);   // turn the LED on

        // Fullcycle step for first motor
            for (i=0; i<fullcycle_theta + 1; i++){
          
                pos1 = pos1_init + i;
                
          
                // Fullcycle step for second motor
                for(j=0; j<fullcycle_phi/4 + 1; j++){
            
                //For even ==> forward, odd, backward //A number is "even" when you can divide it by two and have zero remainder
                    if ((i % 2) == 0) {
                        digitalWrite(pin2Dir, HIGH); pos2 = pos2_init + j;} 
                    else {
                        digitalWrite(pin2Dir,  LOW); pos2 = fullcycle_phi/4 - j;}
                    //pos2 = pos2_init + j;
            
                    // Read the value from the sensor
                    dist = sensor.readRangeSingleMillimeters();
            
                    // Display real degree, and not step value
                    pos1r = pos1 * resol;   pos2r = pos2 * resol;
                    String stringpos     = pos1r + separator + pos2r + separator + dist;
                    Serial.println(stringpos);         
          
                    digitalWrite(pin2Step, HIGH);
                    delayMicroseconds(mydelay);
                    digitalWrite(pin2Step, LOW);
                    delayMicroseconds(mydelay);
                } // Fullcycle step for second motor
                
                digitalWrite(pin1Dir, HIGH); // Direction forward
                digitalWrite(pin1Step, HIGH);
                delayMicroseconds(mydelay);
                digitalWrite(pin1Step, LOW);
                delayMicroseconds(mydelay);
                
                // Emergency break
                action=Serial.readString();         //Read user input into action
                if (action == "X"){
                    homing(i, j);
                    break;
                }
                //Serial.println("");       
            }   // Fullcycle step for first motor
                digitalWrite(led, LOW); Serial.println(""); Serial.println("Job done !");
                homing(i, j);
        }
    }
else {Serial.println("What do you mean ???");}
}

void homing(int cycle_theta, int cycle_phi){
    int i = 0;
    int j = 0;
    Serial.println("Coming Back");
    // Start Homing procedure of Stepper Motor at startup
    delay(delaybackward);
    Serial.println("Start Homing procedure of Stepper Motors at origin");
      
    // Direction modification
    digitalWrite(pin1Dir, LOW); // Direction backward
    digitalWrite(pin2Dir, LOW); // Direction backward
      
    for(i=0; i<cycle_theta; i++){
        String stheta     = "theta ";
        pos1r = (cycle_theta - i) * resol;
        String postheta   = stheta + pos1r;
//        Serial.println(postheta); // XXXDebug
        digitalWrite(pin1Step, HIGH);
        delay(delay_switch);
        digitalWrite(pin1Step, LOW);
        delay(delay_switch);
    }
      
    for(j=0; j<cycle_phi; j++){
    //For even ==> forward, odd, backward //A number is "even" when you can divide it by two and have zero remainder
        if ((cycle_phi % 2) == 0) 
            {digitalWrite(pin2Dir, LOW);} 
        else 
            {digitalWrite(pin2Dir, HIGH);}
      
        String sphi = "phi ";
        pos2r = (cycle_phi - j) * resol;
        String postheta   = sphi + pos2r;
//        Serial.println(postheta); // XXXDebug
    
        digitalWrite(pin2Step, HIGH); delayMicroseconds(mydelay);; digitalWrite(pin2Step, LOW); delayMicroseconds(mydelay);;
    }
    digitalWrite(pin1Dir, LOW); digitalWrite(pin1Step, LOW); digitalWrite(pin2Dir, LOW); digitalWrite(pin2Step, LOW);
}

void microstepping_config(int microstep_pin){
    // Initialisation of MS1&MS2
    if (microstep_pin==1){
        digitalWrite(pin1MS1, LOW);
        digitalWrite(pin1MS2, LOW);
        digitalWrite(pin2MS1, LOW);
        digitalWrite(pin2MS1, LOW);
    }
  
    if (microstep_pin==2){
        digitalWrite(pin1MS1, HIGH);
        digitalWrite(pin1MS2, LOW);
        digitalWrite(pin2MS1, HIGH);
        digitalWrite(pin2MS1, LOW);
    }  
  
    if (microstep_pin==4){
        digitalWrite(pin1MS1, LOW);
        digitalWrite(pin1MS2, HIGH);
        digitalWrite(pin2MS1, LOW);
        digitalWrite(pin2MS1, HIGH);
    }
  
  if (microstep_pin==8){
        digitalWrite(pin1MS1, HIGH);
        digitalWrite(pin1MS2, HIGH);
        digitalWrite(pin2MS1, HIGH);
        digitalWrite(pin2MS1, HIGH);
    }
}

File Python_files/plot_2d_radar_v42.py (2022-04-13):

#!/usr/bin/env python3
# -*- coding: utf-8 -*-
"""
###############################################
##title              :one_stepper_rotation_v01.ino
##description        :Control stepper motors with A4988 and TOF with VL5353LXX-V2
##author             :John Bigeon  (https://github.com/JohnBigeon/PinAr_Lidar)
##date               :20220406
##version            :for arduino MEGA (tested on 1.8.19 @ubuntu)    
##usage              :
##script_version     :0.9-release
##Output             :2D scanning
##notes              :
###############################################
"""

###############################################
# Import libraries
from numpy import *
from pyqtgraph.Qt import QtGui, QtCore
import pyqtgraph as pg
import serial
import os, sys
import matplotlib
import numpy as np
import time
from drawnow import *
from tqdm import tqdm #progress bar

###############################################
# OS used
if os.name == 'posix':
    portName = '/dev/ttyACM0'     # replace this port name by yours!
else :
    portName = 'COM4'         # Windows port
    
###############################################
# Create object serial port
baudrate = 9600
ser = serial.Serial(portName, baudrate, timeout=None)
ser.flushInput()

###############################################
microstepping = 1
step_full_theta = int(200*microstepping/2)
step_theta = int(step_full_theta/2)

### START QtApp #####
#app = QtGui.QApplication([])            # you MUST do this once (initialize things)

###############################################
#   Open a window to display your information
win = pg.GraphicsWindow(title="Signal from serial port") # creates a window
p = win.addPlot(title="Realtime plot")  # creates empty space for the plot in the window
curve = p.plot(pen='g', name='red plot')                        # create an empty "plot" (a curve to plot)
# Add polar grid lines
p.hideAxis('bottom')
p.hideAxis('left')
p.addLine(x=0, pen=0.2)
p.addLine(y=0, pen=0.2)

# Display circle with different diameters
for r in range(2, 300, 100):
    circle = pg.QtGui.QGraphicsEllipseItem(-r, -r, r*2, r*2)
    circle.setPen(pg.mkPen(0.2))
    p.addItem(circle)

windowWidth = 1200                       # width of the window displaying the curve
Xm = linspace(0, 0, windowWidth)          # create array that will contain the relevant time series     
ptr = -windowWidth                      # set first x position

###############################################
#pre-load dummy data
values = []
values = [0] * step_theta

###############################################
def update():
    """
    Realtime data plot. Each time this function is called, the data display is updated
    """
    global curve, ptr, Xm, cnt, sens, values  

    theta = np.linspace(np.pi, 2 * np.pi, step_theta)

###############################################
    # Indicate the counts and the direction
    if (cnt==step_theta):
        sens = -sens
        cnt = 0
    print("Counts & direction: ", cnt, sens)

###############################################
    # Decode the incoming data
    try:
        decoded_bytes = ser.readline().decode('utf-8')[:-1]
    except:
        print(" I missed this one")
        pass        
    print(decoded_bytes)

###############################################
    # Convert to int
    try:
        int_lst = [float(x) for x in decoded_bytes.split(',')]
    except:
        print("not ok")
        int_lst = [0, 0, 0]       
    print ("Distance: ", int_lst[-1])
    Xm[-1-cnt] = int_lst[-1]

###############################################
    if (sens<0):
        values[-cnt] =int_lst[-1]  
    else:
        values[cnt] =int_lst[-1]

###############################################
    # Transform to cartesian and plot
    x = values * np.cos(theta)
    y = values * np.sin(theta)
    curve.setData(x, y)                     # set the curve in polar chart
    cnt=cnt+1
    QtGui.QApplication.processEvents()    # you MUST process the plot now

###############################################
### MAIN PROGRAM #####   
time.sleep(2)   #takes some time to initiate the port
ser.write(b'F')
time.sleep(2)
ser.flushInput()     #flush your input buffer

###############################################
cnt=0
sens=1

if __name__ == "__main__":
    while True: 
        try: 
            update()
        except:
            print("Error loading")
            ser.write(b'X') # emergency case of Arduino
            ser.close() 
            win.close()
            # Let's the LIDAR coming at the start position
            print("finish, lets coming back")
            for i in tqdm(range(10)):
                time.sleep(1)
                pass
            #break
            sys.exit()
    #f.close()
    
    ### END QtApp ####
    pg.QtGui.QApplication.exec_() # you MUST put this at the end
    ##################
